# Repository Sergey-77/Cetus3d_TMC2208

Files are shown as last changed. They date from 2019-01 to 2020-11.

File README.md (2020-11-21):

#        Cetus3d_TMC2208

     This is TMC2208 stepstick drivers extension board for Cetus3d mk3 printer.
Original stepper drivers in Cetus3d printer are set for 32 microsteps, so I added Attiny85 to configure trinamic drivers for 32 microsteps. By default current is set by adjusting referense voltage with the potentiometer. It also can be set by Attiny's firmware, but only for same current for all axis in four steppers version. Three steppers version has separate serial connections to drivers, so current can be set for each motor individualy. My printer has stepper motors with 31 ohms coil resistance, so current has to be set low. Can't find any information about cetus motors. I think maximum current should be no more than 400mA. Reference voltage on my printer is set to: x 0.15v, y 0.1v, z 0.2v. I left extruder on original driver since it's not that loud anyway.</br>
     Printed board can be made with tonner transfer method since it's simple one sided design. Attiny was programmed with Arduino IDE. Motor pins on stepsticks were soldered pointing upward to get original connectors to fit. Also jumper needs to be installed on back of trinamic driver to get chip's serial connected to pin #5(PDN).</br>
     After board was installed it was hard to put cover back on. I had to remove spacer on power switch to slide cover back in place. Modified spacer can be installed after cover was installed. Also needs some insulation  between bottom of exension board and cover to prevent short circuit.

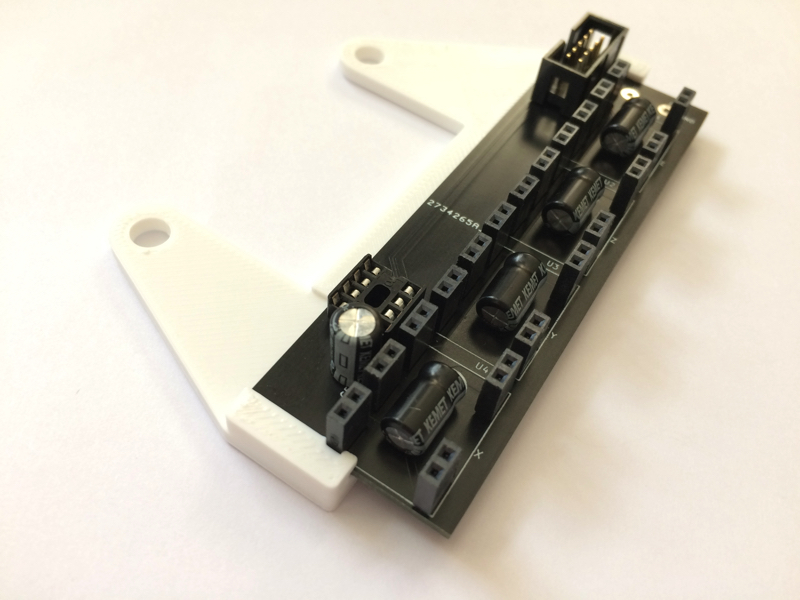
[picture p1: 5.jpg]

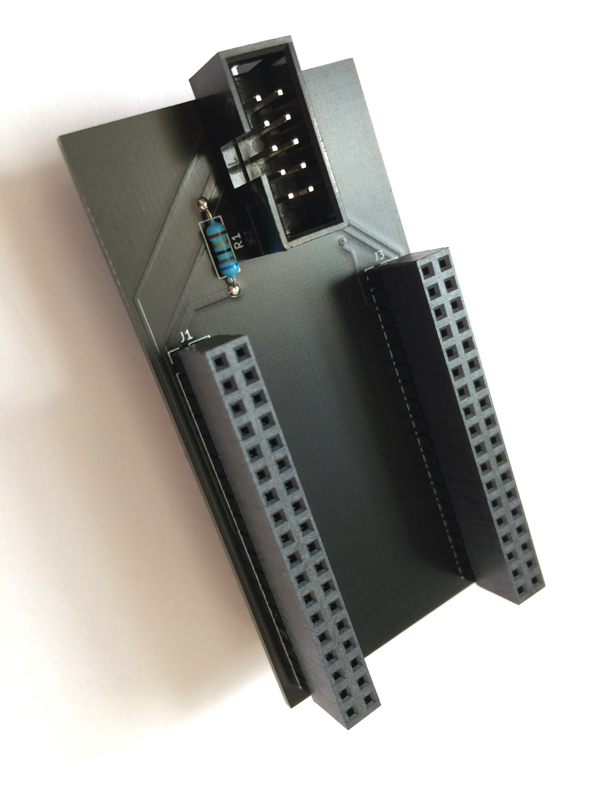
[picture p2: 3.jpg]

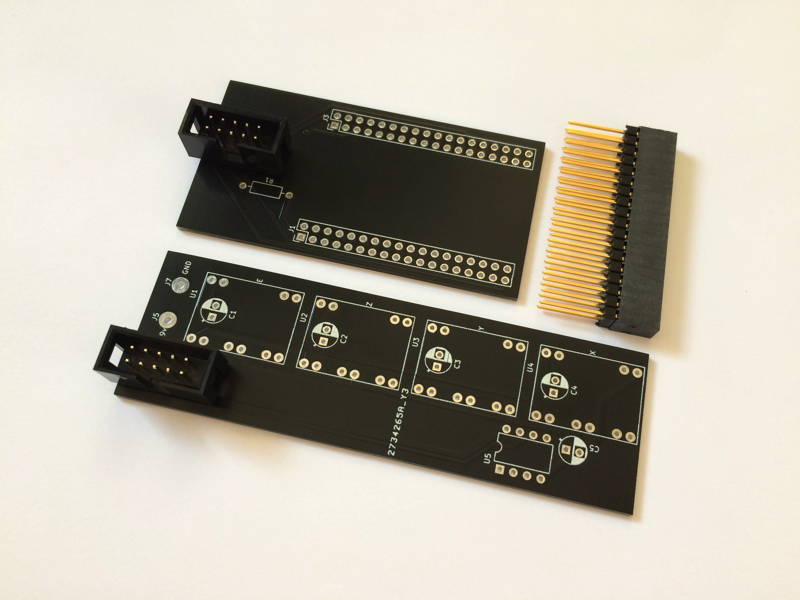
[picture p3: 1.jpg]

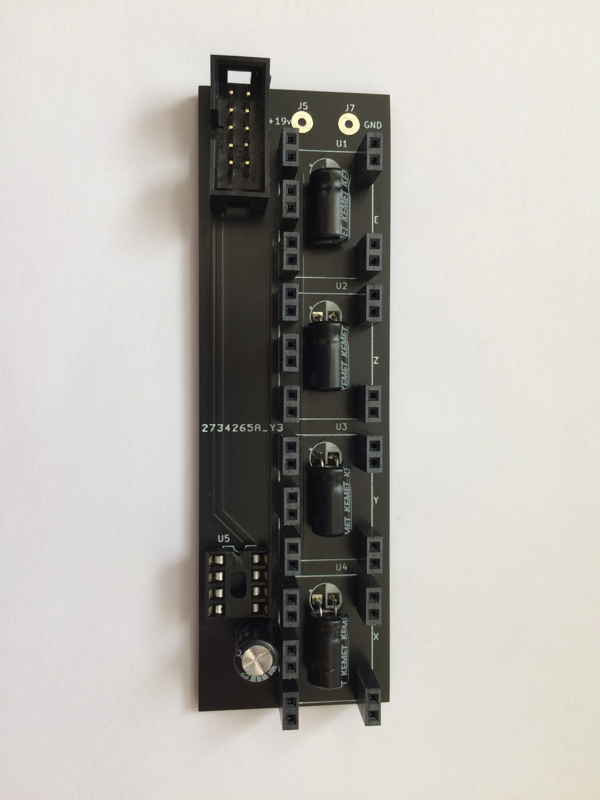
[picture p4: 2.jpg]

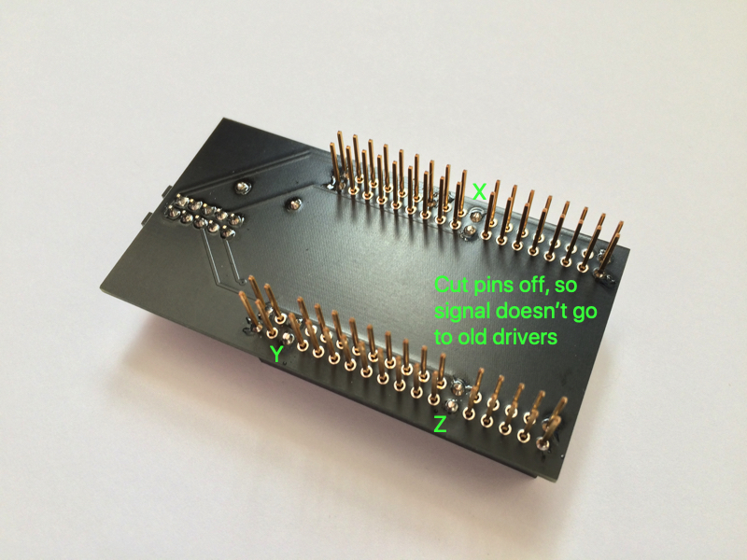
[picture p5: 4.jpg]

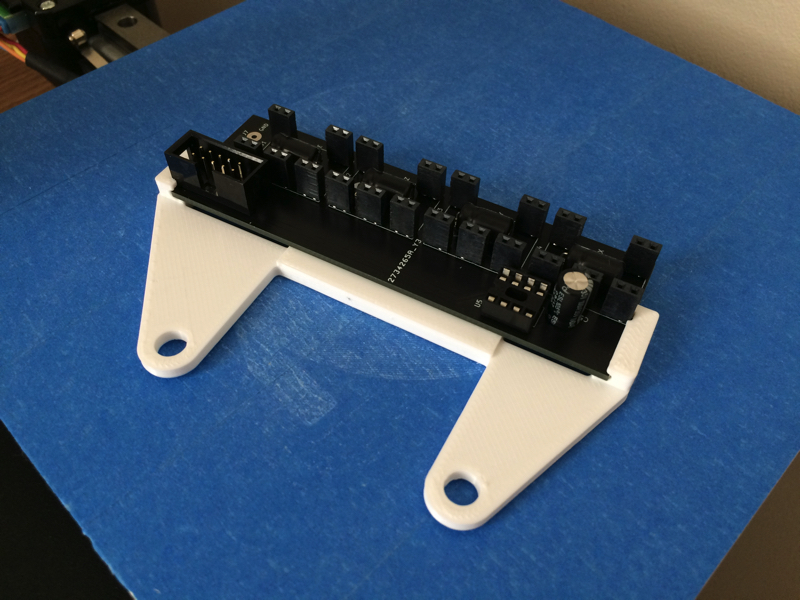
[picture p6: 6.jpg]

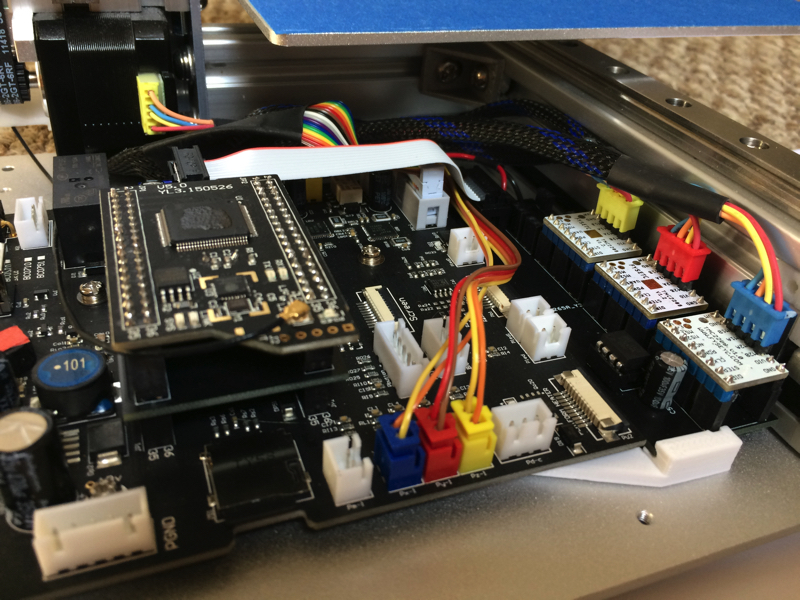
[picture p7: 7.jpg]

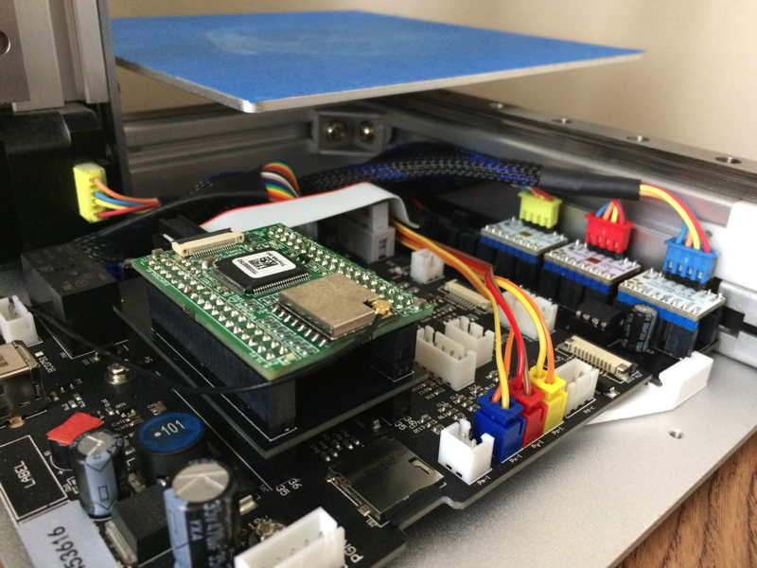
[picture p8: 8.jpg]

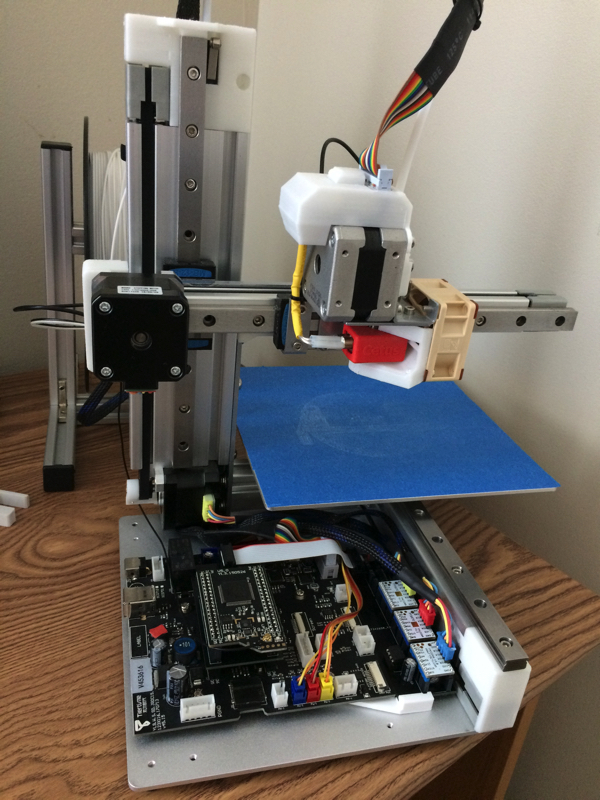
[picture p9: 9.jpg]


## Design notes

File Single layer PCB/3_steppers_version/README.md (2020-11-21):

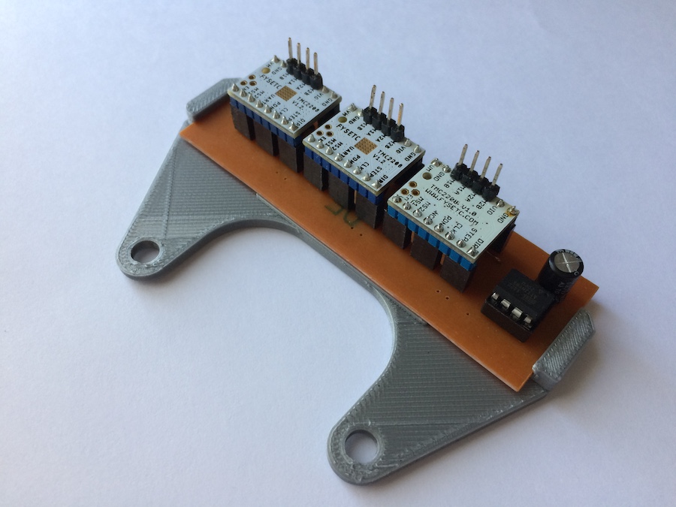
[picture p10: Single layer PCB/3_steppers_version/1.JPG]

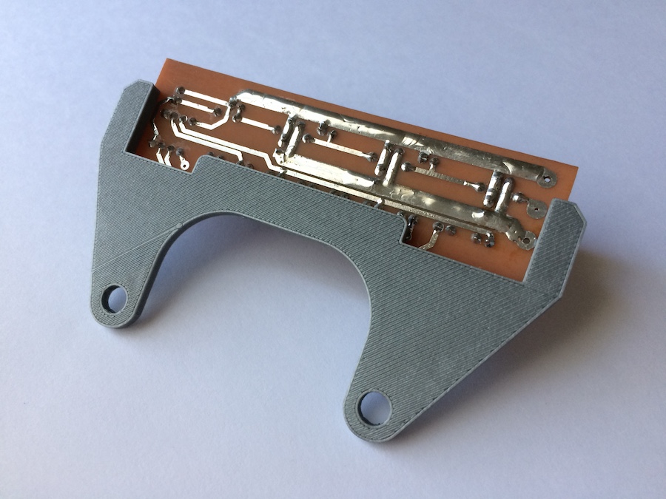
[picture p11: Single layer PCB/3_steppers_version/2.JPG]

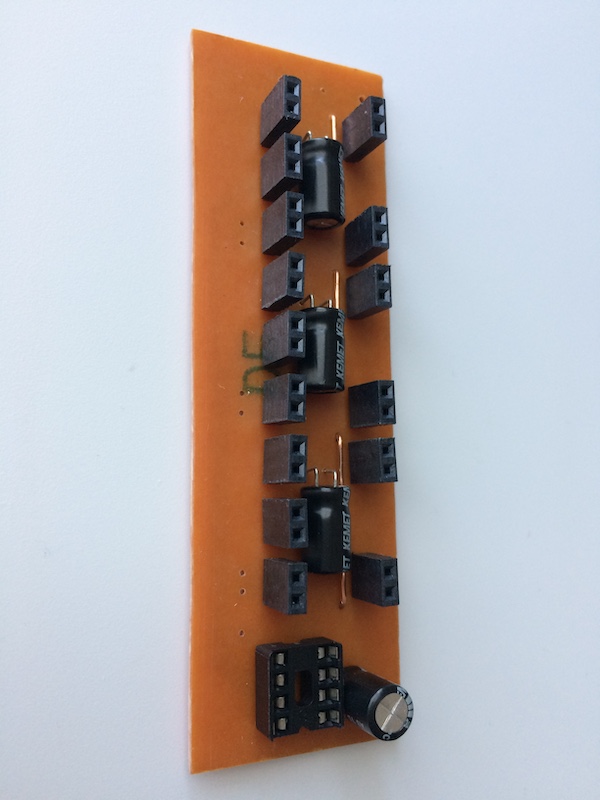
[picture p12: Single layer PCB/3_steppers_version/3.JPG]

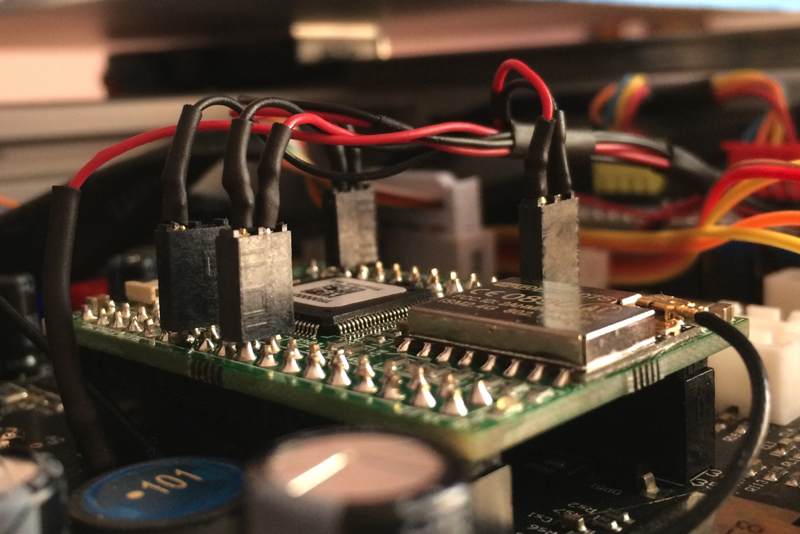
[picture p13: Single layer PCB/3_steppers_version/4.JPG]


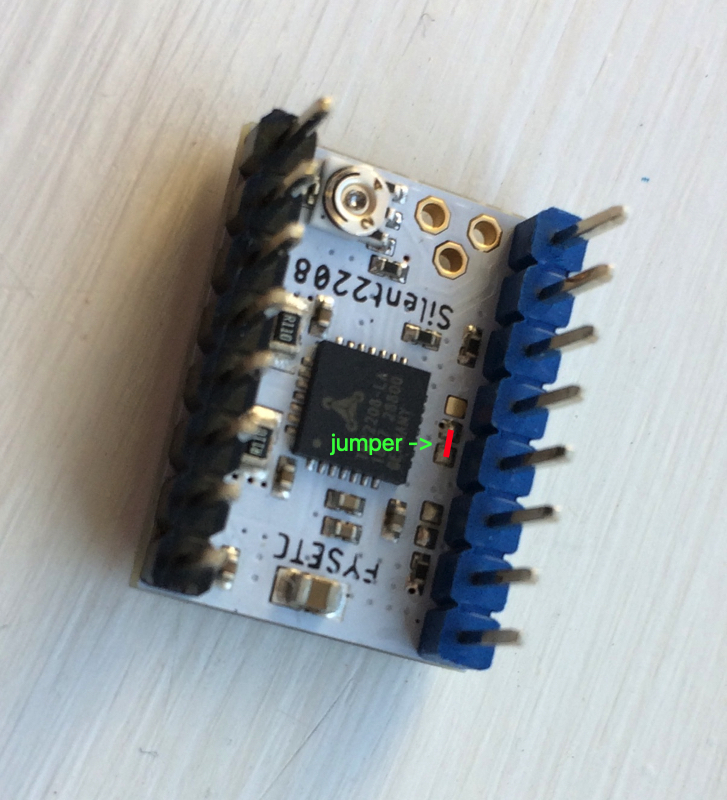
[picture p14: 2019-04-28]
jumper.jpg

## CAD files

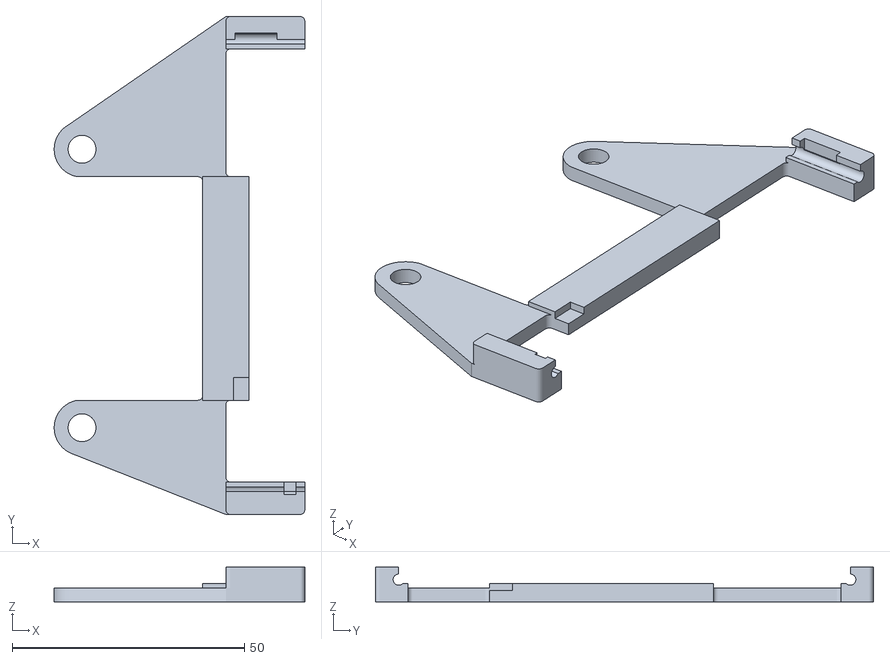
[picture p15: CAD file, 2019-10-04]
cetus_pcb_bracket.stl
54.0 x 107.3 x 7.50

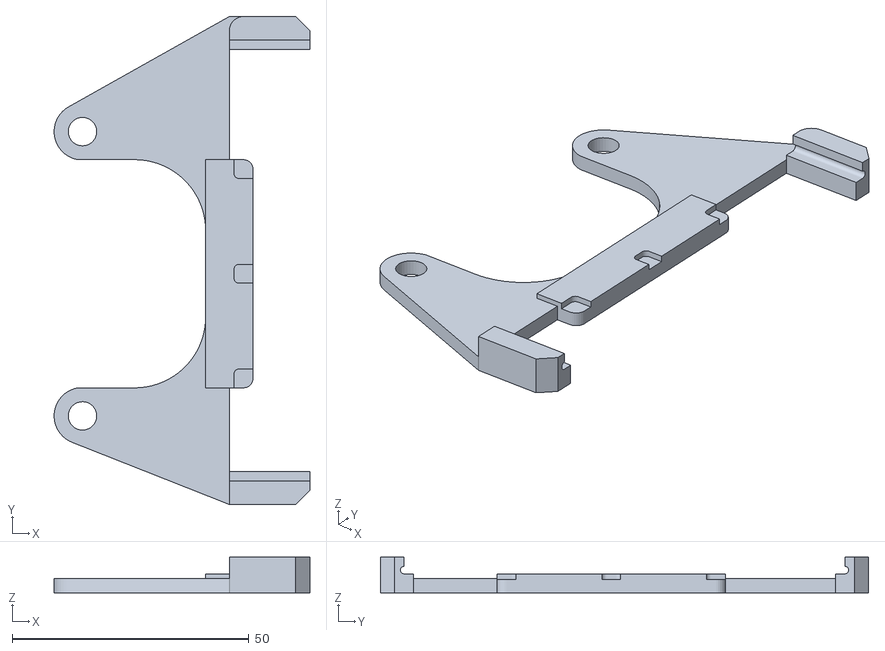
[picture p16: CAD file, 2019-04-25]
Single layer PCB/3_steppers_version/cetus_pcb_bracket_v2.stl
54.0 x 103.0 x 7.50

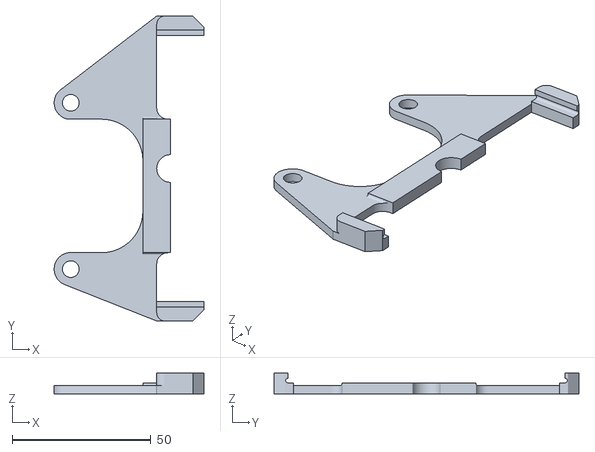
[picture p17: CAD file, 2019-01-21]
Single layer PCB/4_steppers_version/cetus_pcb_bracket.stl
54.0 x 110.0 x 7.50

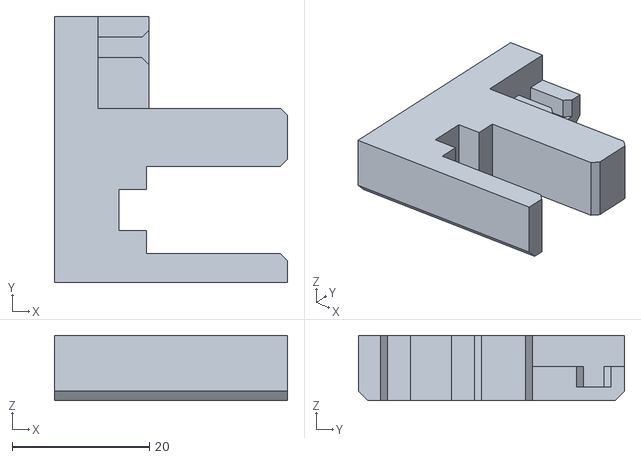
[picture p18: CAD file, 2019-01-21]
cetus_power_switch_spacer.stl
33.9 x 38.7 x 9.50

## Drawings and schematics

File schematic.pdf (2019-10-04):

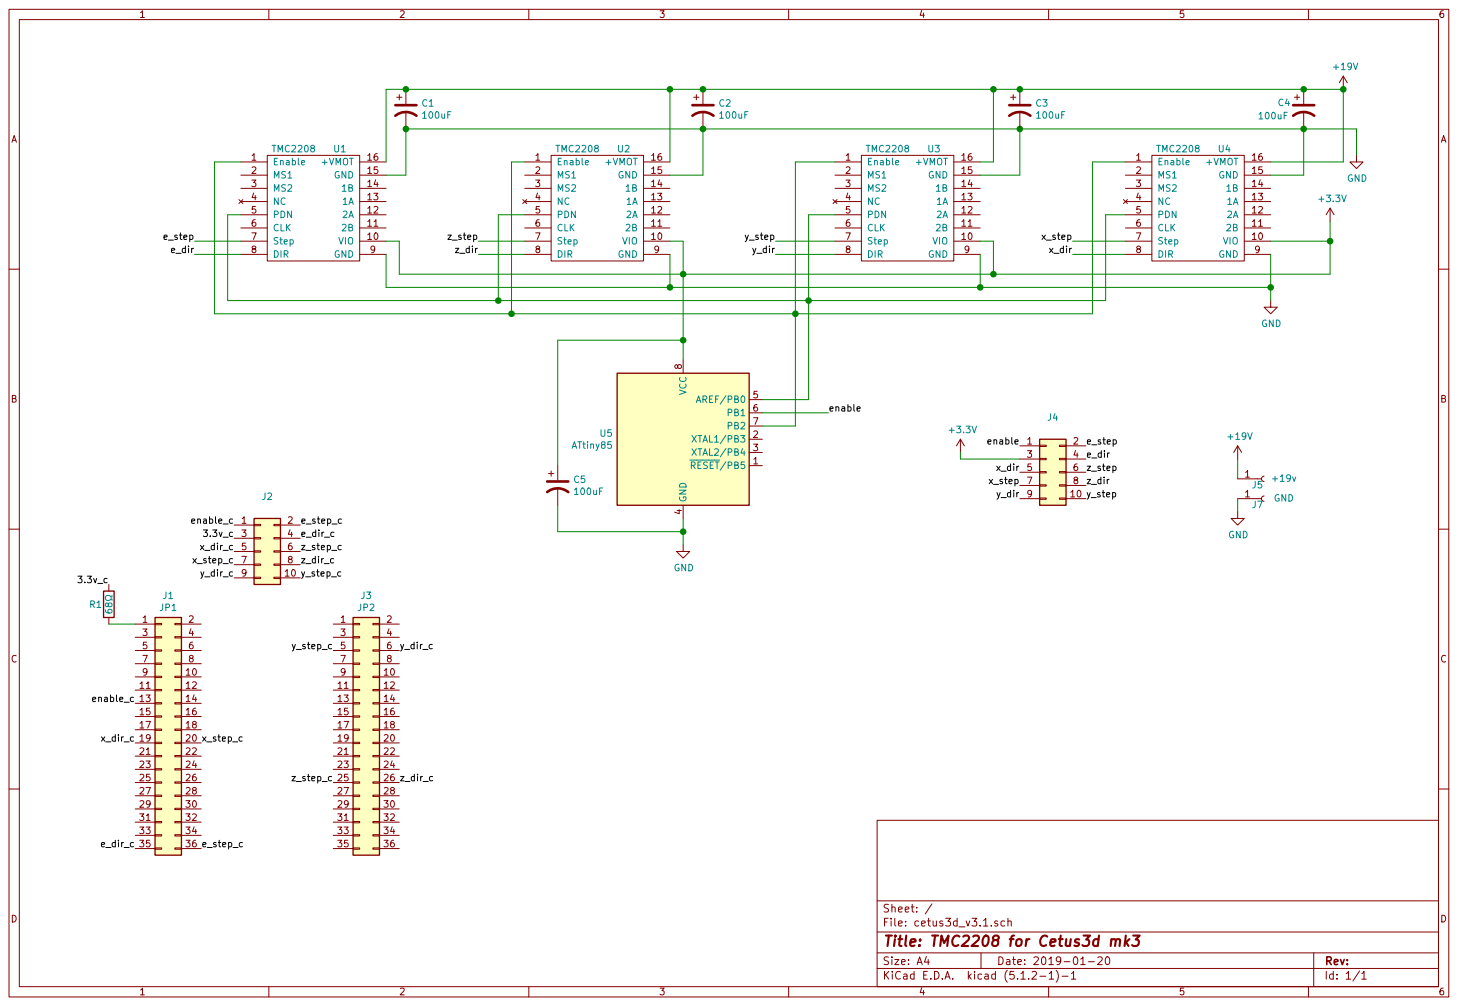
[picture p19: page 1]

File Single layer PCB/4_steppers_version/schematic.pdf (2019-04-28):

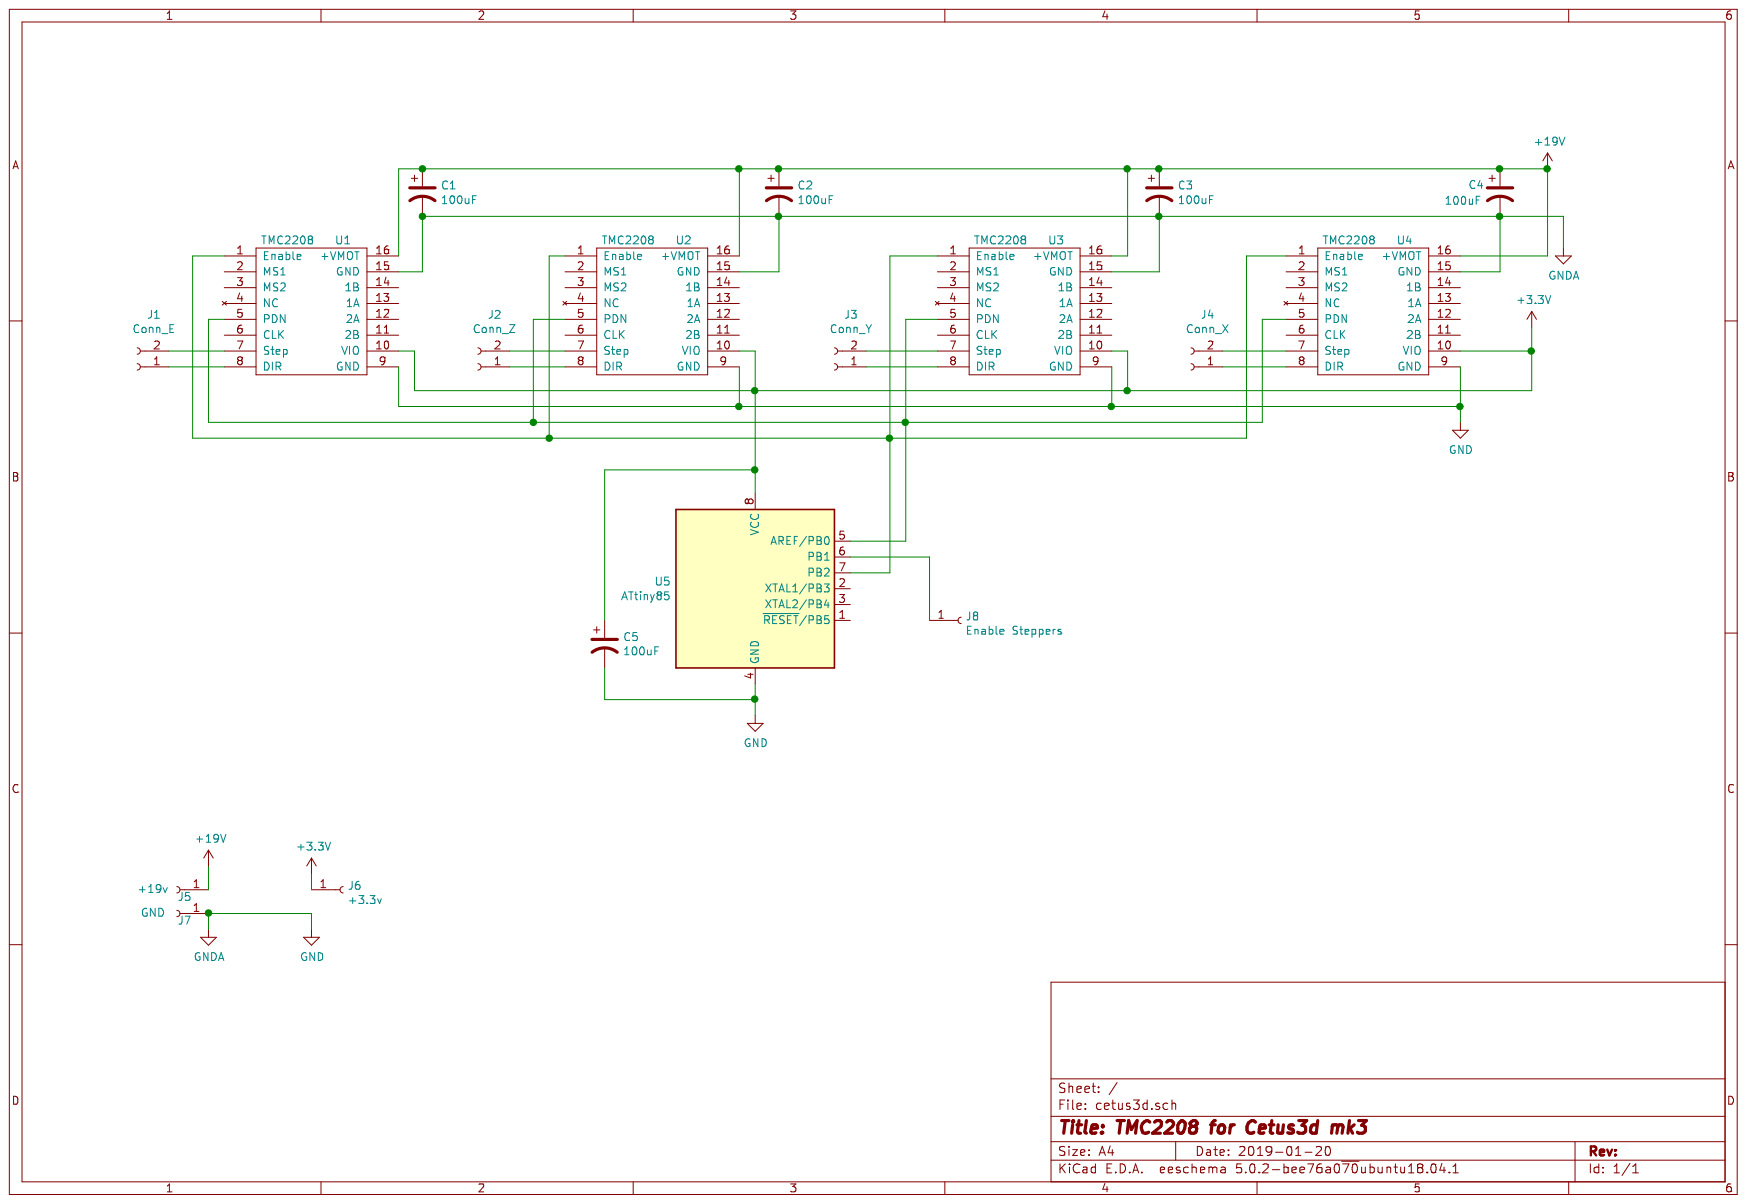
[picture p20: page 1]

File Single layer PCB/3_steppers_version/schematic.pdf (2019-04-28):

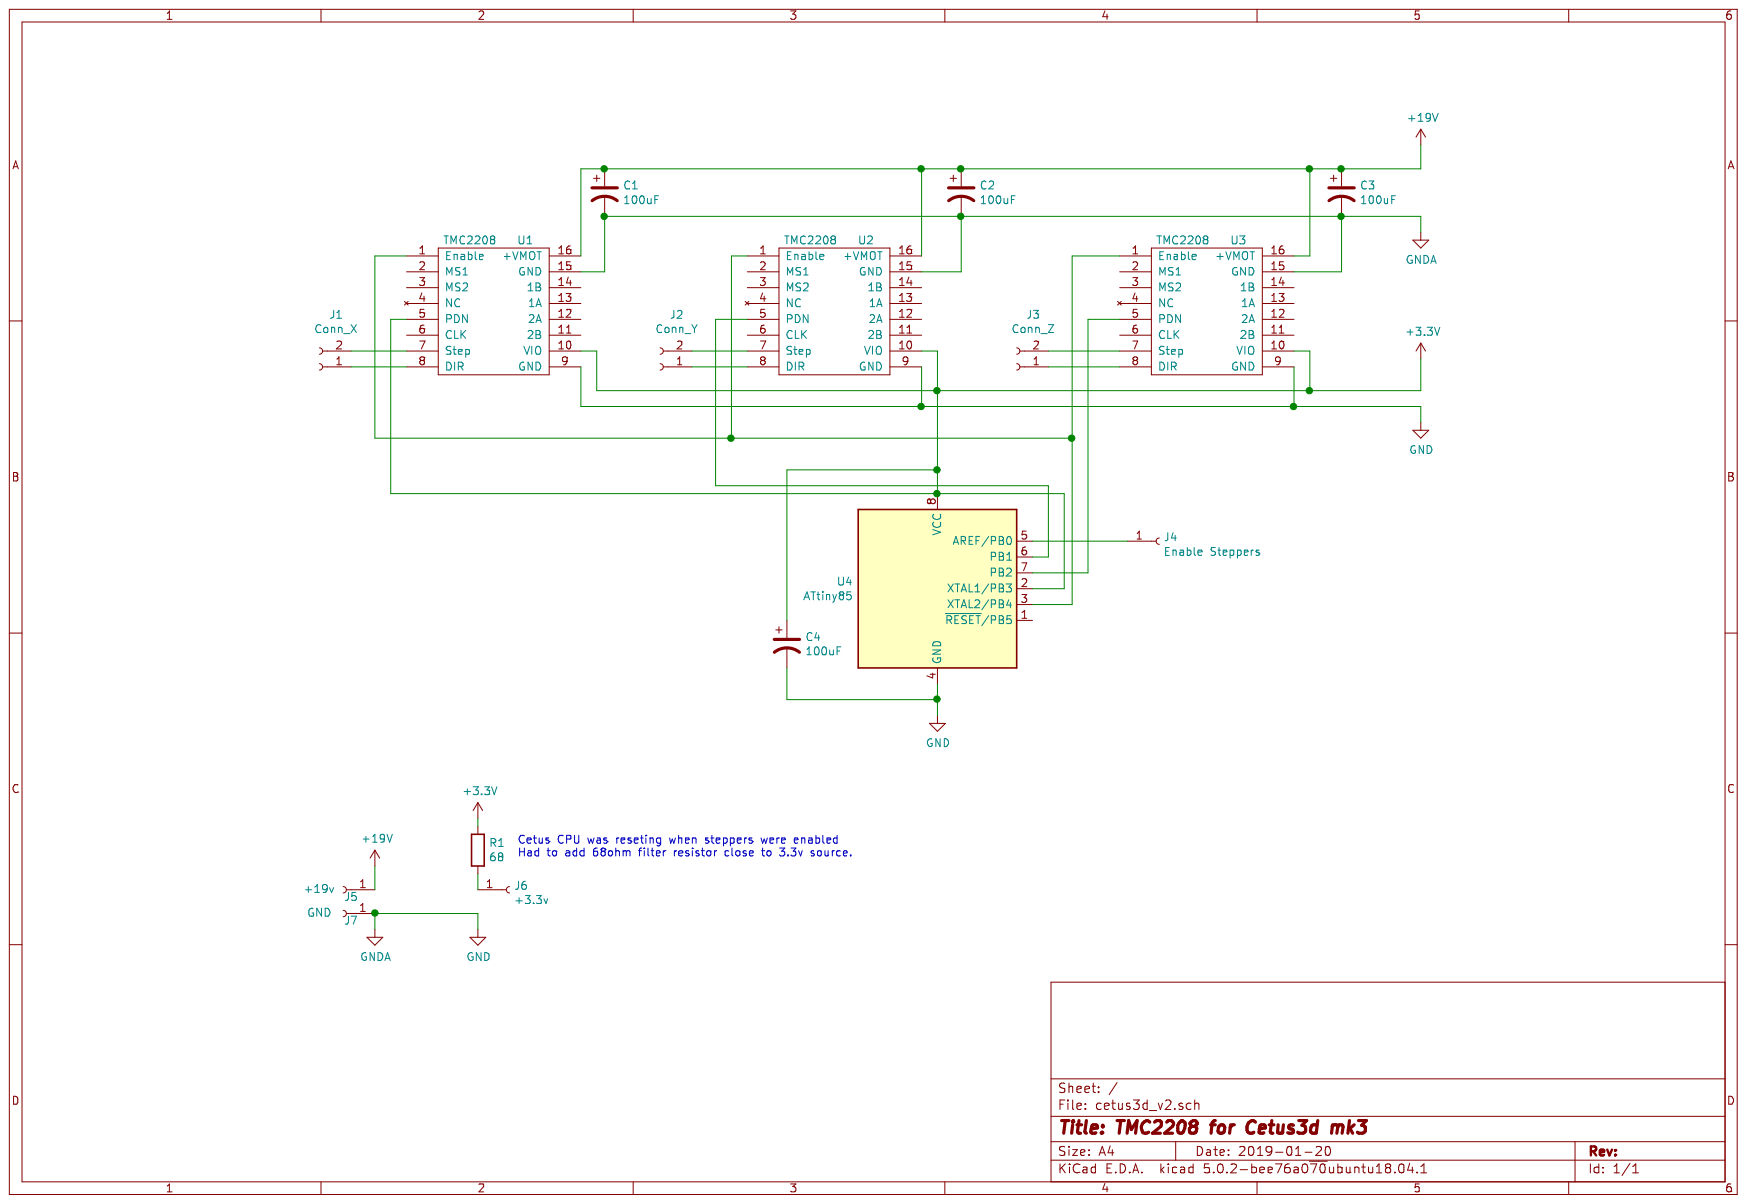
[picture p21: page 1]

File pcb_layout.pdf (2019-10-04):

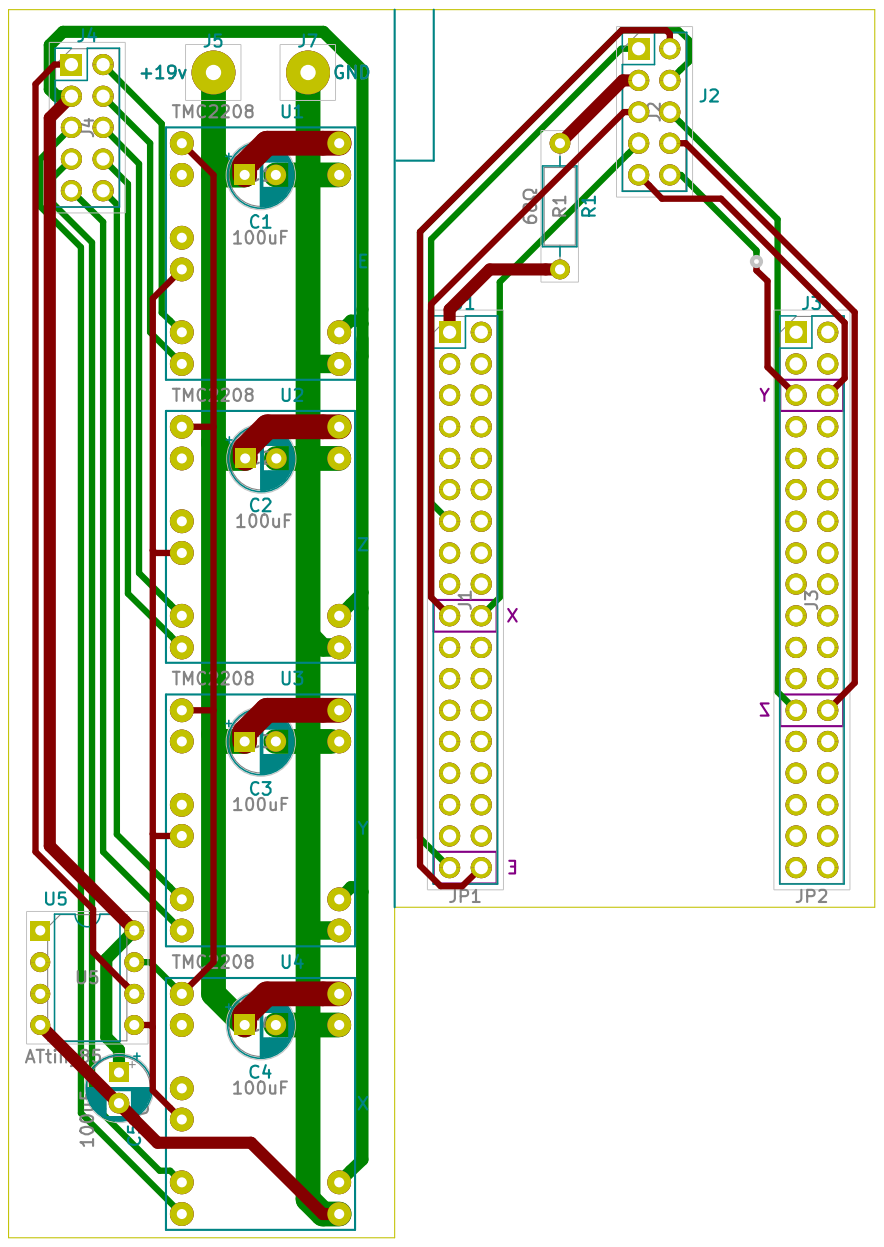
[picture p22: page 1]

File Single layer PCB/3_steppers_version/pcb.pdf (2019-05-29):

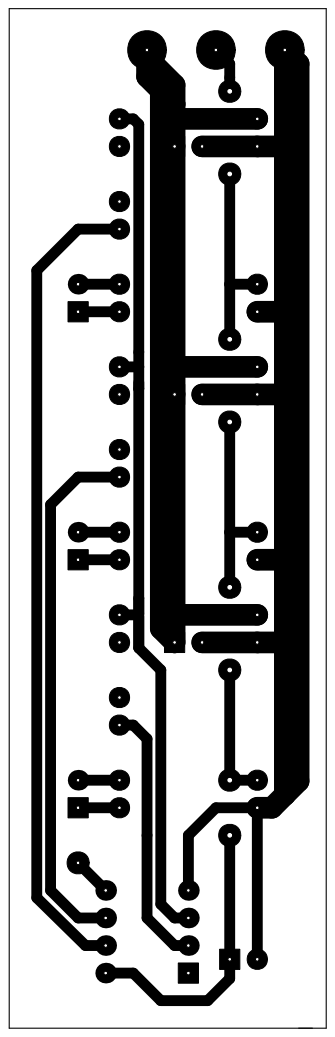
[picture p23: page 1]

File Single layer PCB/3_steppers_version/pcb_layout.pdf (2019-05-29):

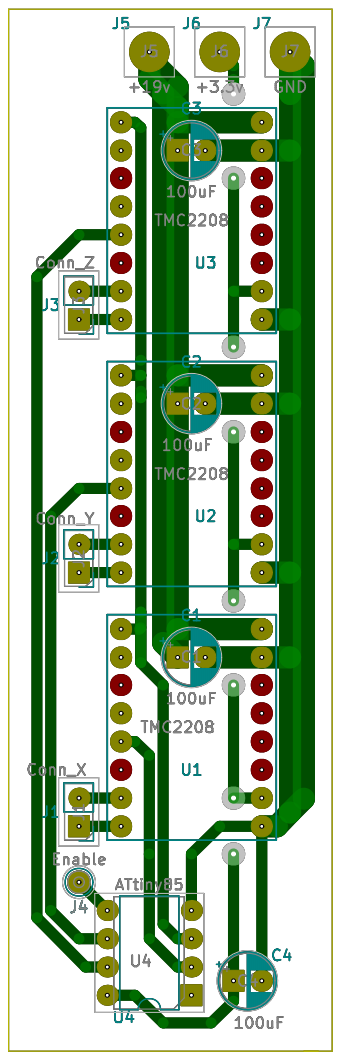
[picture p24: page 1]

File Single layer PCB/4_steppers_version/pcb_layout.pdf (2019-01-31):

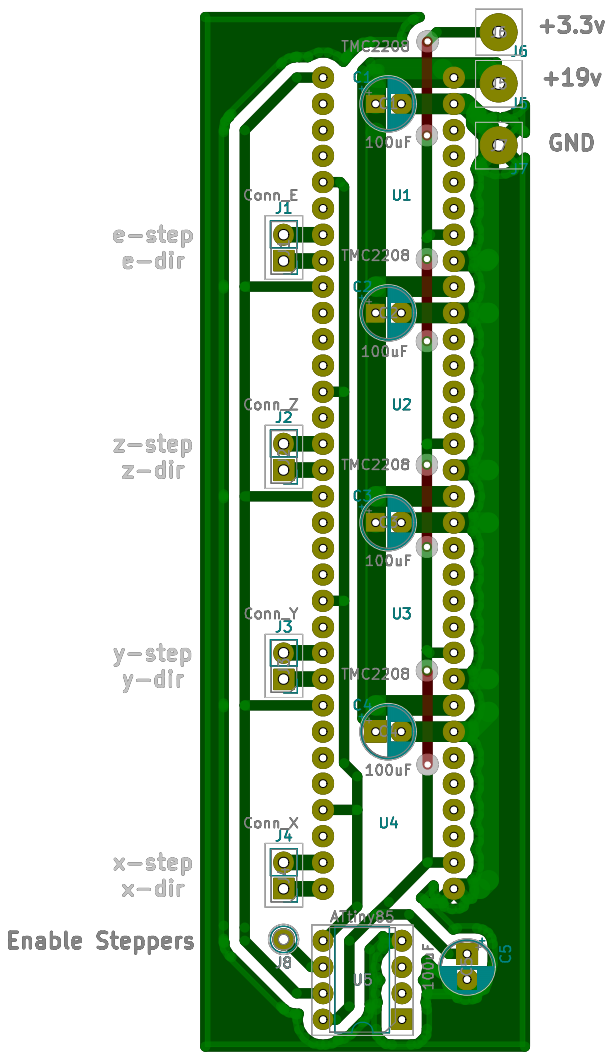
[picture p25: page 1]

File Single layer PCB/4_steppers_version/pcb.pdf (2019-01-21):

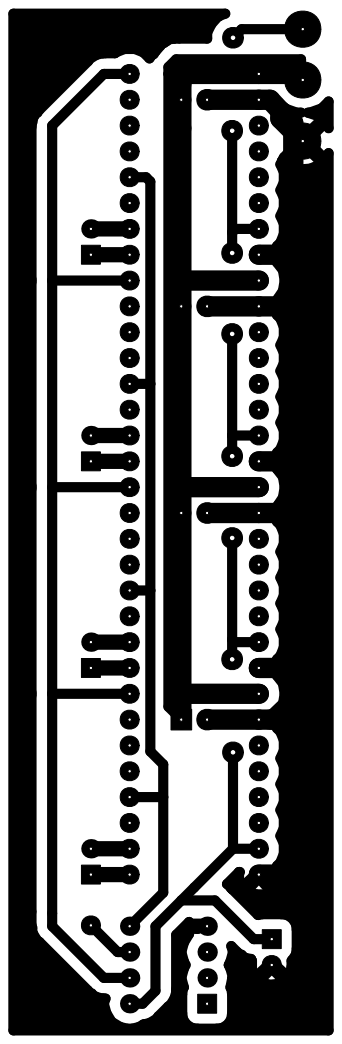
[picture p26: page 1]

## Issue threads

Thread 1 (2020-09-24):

TMC_2208 connections

vinnyJager, 2020-09-24:
Hi,

I've got a question about image number 7, double layer pcb. The the stepper drivers connect into the female headers, soldered on to one of the PCB's included in this project. So I'm wondering why is there a cable from the Cetus also connected to the stepper drivers but from above.
And I'm wondering what connectors you use on the pcb's, is there a parts list or something?

Kind regards,
Vincent

Sergey-77, 2020-11-21:
Index | Quantity | Part Number | Manufacturer Part Number | Description
-- | -- | -- | -- | --
1 | 2 | SAM9312-ND | ESQ-118-14-G-D | CONN SOCKET 36POS 0.1 GOLD PCB
2 | 1 | 3M157849-1-ND | 3365/10 100 | CBL RIBN 10COND 0.050 GRAY 1’
3 | 2 | S9286-ND | SFH210-PPPC-D05-ID-BK | CONN HEADER 10POS IDC 28AWG GOLD
4 | 2 | S9169-ND | SBH11-PBPC-D05-ST-BK | CONN HEADER VERT 10POS 2.54MM

Got connectors from DigiKey. 36 pin connector’s pins were too long. I think SSQ-118-03-G-D would be better choice.

Pins for stepper motor were soldered on top of stepper driver, not on bottom as rest of the pins. Cable from motor connected directly to driver through those pins.

Closed 2020-11-25.

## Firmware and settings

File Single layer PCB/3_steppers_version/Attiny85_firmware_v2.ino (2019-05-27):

// Needs TMC2208Stepper library by teemuatlut
#include <TMC2208Stepper.h>
// Define pins
#define EN_PIN 4  // LOW: Driver enabled. HIGH: Driver disabled
#define rxPin 5
#define txPin_x 3
#define txPin_y 1
#define txPin_z 2
#define input_enable_motors 0

void setDriversInternal_ref(int current_mA, TMC2208Stepper *driver){
  driver->push();                // Reset registers
  driver->pdn_disable(true);     // Use PDN/UART pin for communication
  driver->mstep_reg_select(true);
  driver->microsteps(32);
  driver->I_scale_analog(false); // Use internal voltage reference
  driver->internal_Rsense(false);
  driver->rms_current(current_mA);// Set driver current
  driver->toff(3);               // Enable driver in software
  driver->blank_time(24);
  driver->intpol(1);
  driver->TPOWERDOWN(128); // ~2s until driver lowers to hold current
  driver->hysterisis_start(3);
  driver->hysterisis_end(2);
  driver->pwm_lim(12);
  driver->pwm_reg(5);
  driver->pwm_autograd(1);
  driver->pwm_autoscale(1);
  driver->pwm_freq(1);
  driver->pwm_grad(14);
  driver->pwm_ofs(36);
  driver->en_spreadCycle(false);
  driver->GSTAT(0b111); // Clear
}

void setDriversExternal_ref(TMC2208Stepper *driver){
  driver->push();                // Reset registers
  driver->pdn_disable(true);     // Use PDN/UART pin for communication
  driver->mstep_reg_select(true);
  driver->microsteps(32);
  driver->IHOLD_IRUN(0x1F10); // Irms = (Vref * 1.768A) / 2.5V = Vref * 0.707
  //driver->IHOLD_IRUN(0x1008);   // Irms = Vref * 0.37565
  driver->I_scale_analog(true);
  driver->internal_Rsense(false);
  driver->toff(3);               // Enable driver in software
  driver->blank_time(24);
  driver->intpol(1);
  driver->TPOWERDOWN(128); // ~2s until driver lowers to hold current
  driver->hysterisis_start(3);
  driver->hysterisis_end(3);
  //driver->pwm_lim(12);
  driver->pwm_autograd(1);
  driver->pwm_autoscale(1);
  driver->pwm_freq(1);
  driver->pwm_reg(5);
  driver->pwm_grad(14);
  driver->pwm_ofs(36);
  driver->en_spreadCycle(false);
  driver->GSTAT(0b111); // Clear
}

void setup() {
  pinMode(input_enable_motors, INPUT);
  pinMode(EN_PIN, OUTPUT);
  digitalWrite(EN_PIN, HIGH);   // Disable driver in hardware
  TMC2208Stepper driver = TMC2208Stepper(rxPin, txPin_x, false);  // Create driver and use Software Serial for communication
  driver.beginSerial(9600);
  //setDriversInternal_ref(100, &driver);     //Stepper current can be set by Attiny 
  setDriversExternal_ref(&driver);            //or with driver potentiometer
  driver = TMC2208Stepper(rxPin, txPin_y, false);
  driver.beginSerial(9600);
  //setDriversInternal_ref(90, &driver);
  setDriversExternal_ref(&driver);
  driver = TMC2208Stepper(rxPin, txPin_z, false);
  driver.beginSerial(9600);
  //setDriversInternal_ref(150, &driver);
  setDriversExternal_ref(&driver);
}

void loop() {
 delay(500);
 if(digitalRead(input_enable_motors)){
  digitalWrite(EN_PIN, LOW);    // Enable driver in hardware
 }
 else {
  digitalWrite(EN_PIN, HIGH);    // Disable driver in hardware
 }
}

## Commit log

2019-05-14 Add files via upload
    Flipped direction and step pins, added enable pin on top side of CPU board.
2019-05-29 added pcb layout
2019-05-29 added pcb
2019-05-29 Flipped direction and step pins, added enable pin on top side of CPU board.
2019-10-04 moved to new directory
    [cetus_pcb_bracket_v2.stl]
2019-10-04 Double layer PCB
    [cetus_pcb_bracket.stl]
2019-10-04 Single layer PCB
    [cetus_pcb_bracket.stl, cetus_pcb_bracket_v2.stl]
2019-10-04 Jumper on TMC Driver
2019-10-04 CPU adapter and driver board as a single board
2019-10-04 added gerber files
